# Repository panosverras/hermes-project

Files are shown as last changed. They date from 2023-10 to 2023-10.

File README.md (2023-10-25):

# HERMES project
WRO2023 Future Innovators project (smartbirds team)

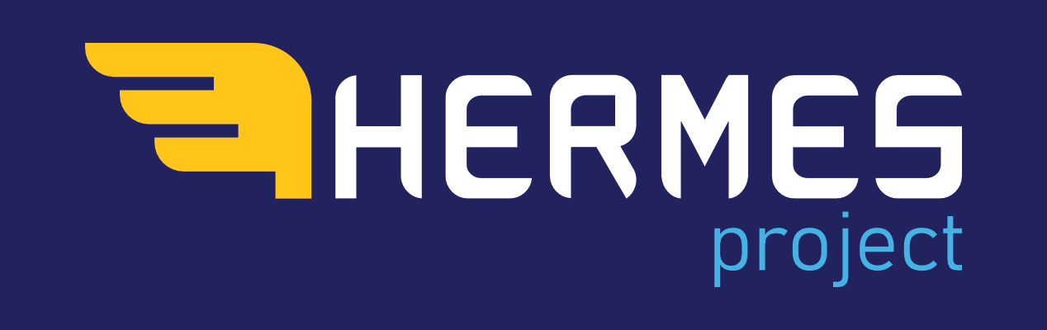
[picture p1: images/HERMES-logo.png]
HERMES logo


HERMES is a project created by **smartbirds** team (Greece) for their participation to the World Robot Olympiad 2023.
Team consists of 3 high school students, Niobe, Thymios, Faidon and their coach Mr. Panos Verras.

You can watch a short introduction of our project [here](https://www.youtube.com/watch?v=-QXrDMuEW-o).

Our project is open-source under the MIT licence. Feel free to copy, modify, reproduce in order to create a better world!

## Why we created HERMES?

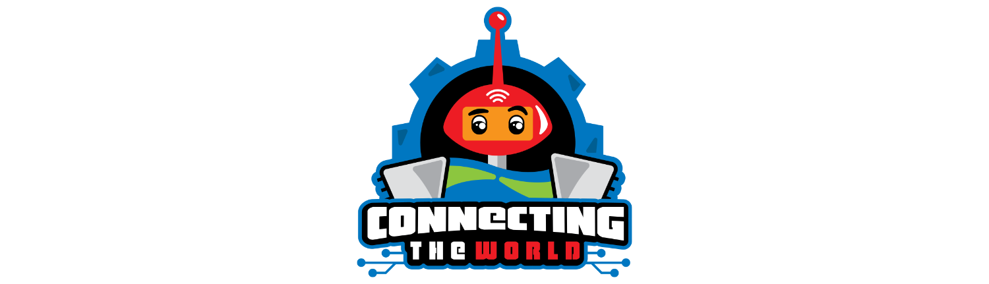
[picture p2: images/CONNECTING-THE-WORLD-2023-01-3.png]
WRO2023 theme - Connecting the World


After lots of research on this season’s theme “Connecting the World”, we came to the idea of HERMES, a multifunctional robotic system that maintains a more stable telecommunication network/infrastructure working as single node (p2p) or in combination with other units (HERMES mesh network). HERMES is based on our research on the fields of today’s IT infrastructure, undersea cable networks, socio-economic impact of IT on our daily life, marine traffic, ship design, underwater and overwater scientific and climate data and UN Sustainability Goals.

Since the beginning of time, waterways have played an important role in human communications, linking geographies and societies far and wide. Today, water not only facilitates transportation and trade but also connects nations and continents across the globe through the worldwide system of computer networks. The internet connects over 5 billion people around the world, with an impressive 99% of data being transferred through undersea fiber-optic cables. Damage on the physical underwater infrastructure could cause a multitude of problems due to internet outage, especially in cases of remote areas where an entire community relies on a few cables or even just one.

Every year, the underwater communication network undergoes between 100 and 150 faults. Most of these cable faults occur in water depths shallower than 200 meters, within a distance of approximately 1000 meters from the coastline. The internet downtime period resulting from cable faults depends on weather and climate conditions and it may take up to several months for a complete repair. Moreover, as global overseas shipping continues to grow and thus traffic in shallower waters surges, cable incidents and pollution will only increase, especially in congestion points, such as canals and rivers.

Loss of internet connectivity presents significant challenges for nations, governments and everyday people. However, the complete absence of internet access in remote regions is equally detrimental. Extending internet access to remote areas ultimately gives these communities access to vital resources and services by helping them connect to the rest of the world.

The problems arising from lack of internet access are numerous and complex, so innovative ideas and advanced technologies are the solution. Our project, HERMES, can help.

HERMES is an innovative robotic solution designed to act as a data bypass link in the event of an undersea cable fault, ensuring uninterrupted data flow. HERMES can also replace the role of underwater fiber-optic cables near the shore and therefore open valuable sea lanes that were restricted to protect those cables. Additionally, HERMES can provide an internet connection to remote regions. The robot also has environmental monitoring functions and other capabilities which focus on its surroundings.

## HERMES key features

**Wireless Network Technology:** The central idea behind this robotic solution is to decrease the possibility of cable damage, by replacing the cable communications with a wireless network, until repaired or permanently.
**Navigation and Bypass:** HERMES is able to navigate to the coordinates of the accident and bypass the communication.
**Network Extender for Remote Areas:** A system that can also run as a network extender for unreachable remote areas.
**Environmental Monitoring:** Additionally, our model operates as a station to collect data and monitor the environment, in order to identify environmental anomalies and spot air and water pollution.
**Safety in water:** Hermes can warn vessels and assist in search and rescue missions by detecting the presence of living organisms.

## How we created HERMES
HERMES system consists of 3 parts, although its name was given by the main vessel. 

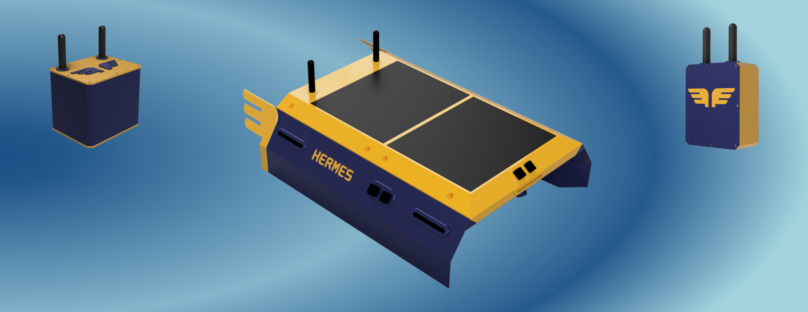
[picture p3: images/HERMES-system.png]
HERMES system


All 3 subsystems where designed in Fusion 360 and 3D printed. Due to restrictions on printing volume but also on our concept of using two colors, these susbsystems consist of several parts. In folder Design/STL you can find all these parts organized by the subsystem name. Using those files you will be able to slice and print an exact copy of HERMES, land station and underwater station. Indicatively, printing time required is more than 200 hours on a low-cost printer (like the one we used). We have rendered a small video demonstrating the assembly steps for the HERMES vessel (find it under Videos folder).

Raspberry Pi PICO is used as the main controller on all subsystems. Especially HERMES included two of them in order to balance proccessing speed and control in a better way all its functionalities. Programming language used is Python and in specific controllers are using [Circuitpython](https://circuitpython.org/) that is a user-friendly python version dedicated to micro-controllers. In folder Code you can find our programs for its one of the subsystems. Please mention that HERMES includes two PICO's so you will find two programs in that folder.

Electronics used are from several manufacturers, depending on their capabilities, their availability and our purpose (present our idea at WRO2023). Below you may find a list of the ones we used and a diagram for their connection.

### HERMES
- 2x Rasperry Pi PICO
- 2x Pico expansion board
- 3x IIC to UART module
- 4x HC12 RF module
- 4x RF waterproof antenna
- 1x PH sensor kit
- 1x Conductivity sensor kit
- 1x DS18B20 waterproof sensor
- 1x TSL2591 sensor
- 1x BME680 sensor
- 1x MQ135 sensor
- 1x GPS module
- 1x BNO 055 Euler angles sensor
- 1x Thernal imaging camera
- 2x Solar panel 3.5W
- 2x Solar power manager 10000mAh
- 1x DC step-down 5v dual usb
- 1x Dual motor driver module
- 2x thruster (dc motor)

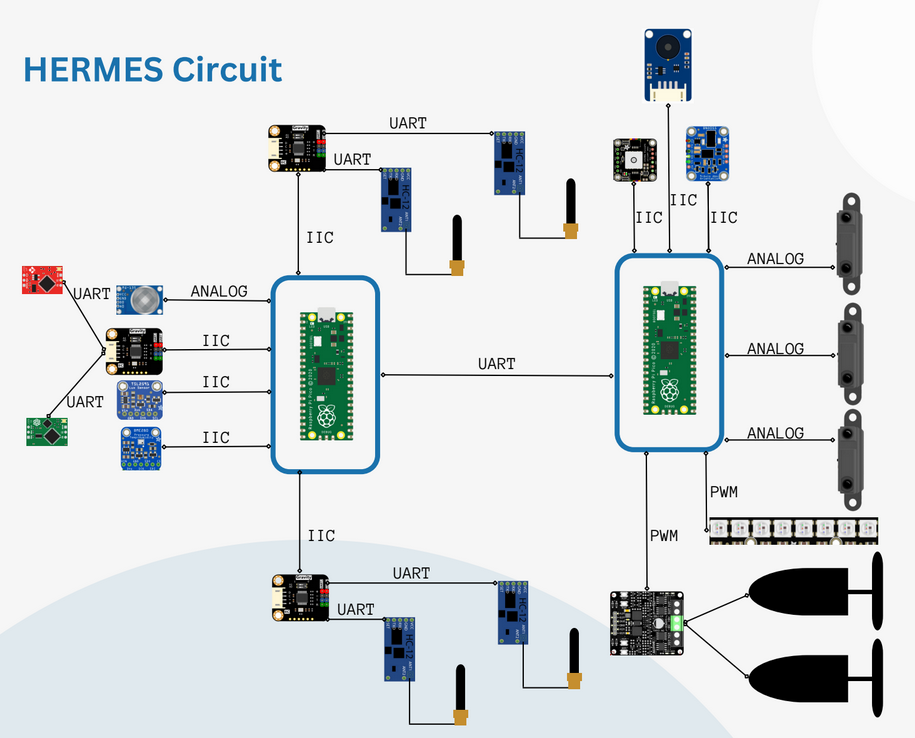
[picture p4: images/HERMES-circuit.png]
HERMES circuit


### LAND station
- 1x Rasperry Pi PICO
- 1x Pico expansion board
- 2x HC12 RF module
- 4x RF waterproof antenna

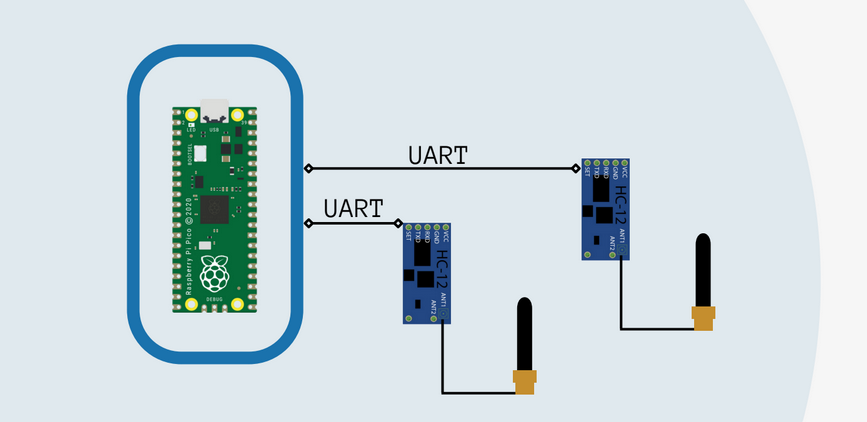
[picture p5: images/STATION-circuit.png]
LAND station circuit


### UNDERWATER station
- 1x Rasperry Pi PICO
- 1x Pico expansion board
- 2x HC12 RF module
- 4x RF waterproof antenna

LAND station circuit

## Innovation and social impact of HERMES
HERMES is a truly innovative addition to today's interconnected society. 

**Safety and Reliability for Users:** HERMES aims to increase the safety and reliability of telecom systems for users, making essential everyday networks more secure and with a steadier infrastructure.

**A Global Transformation:** Our vision is to alter worldwide communications for the better, by establishing the most stable transmission system ever. 

**Rapid Deployment and Integration:** Being a low cost and open source project it allows the rapid deployment and integration into the global internet infrastructure.

Humankind now can rely on this stable communication network for critical sectors of daily life such as good health and well being (goal 3), quality education (goal 4), reduced inequalities (goal 10), decent work and economic growth (goal 8) and many more.

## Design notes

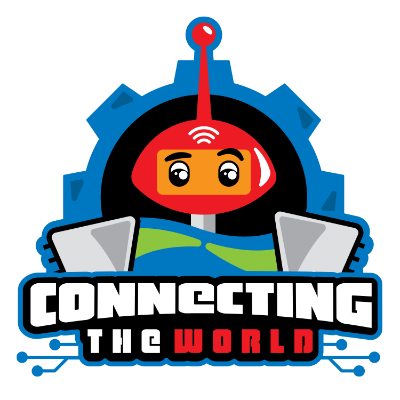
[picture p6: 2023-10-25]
images/CONNECTING-THE-WORLD-2023-01-1.png

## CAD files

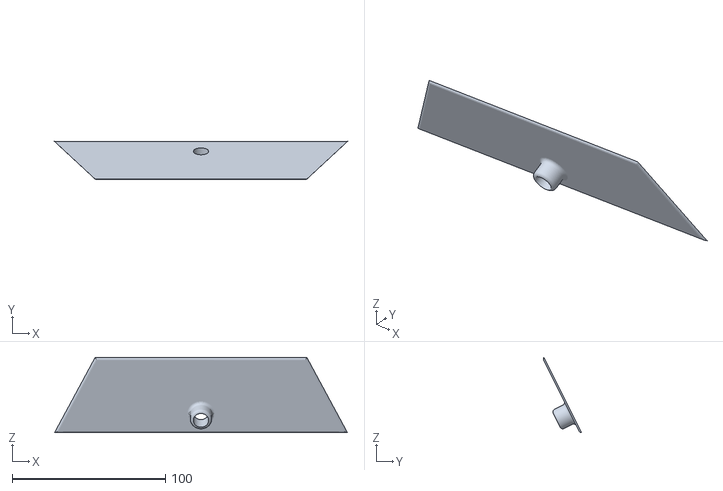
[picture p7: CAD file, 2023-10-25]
Design/STL/HERMES/BRIDGE/FRONT-MASK.stl
191.1 x 24.9 x 49.1

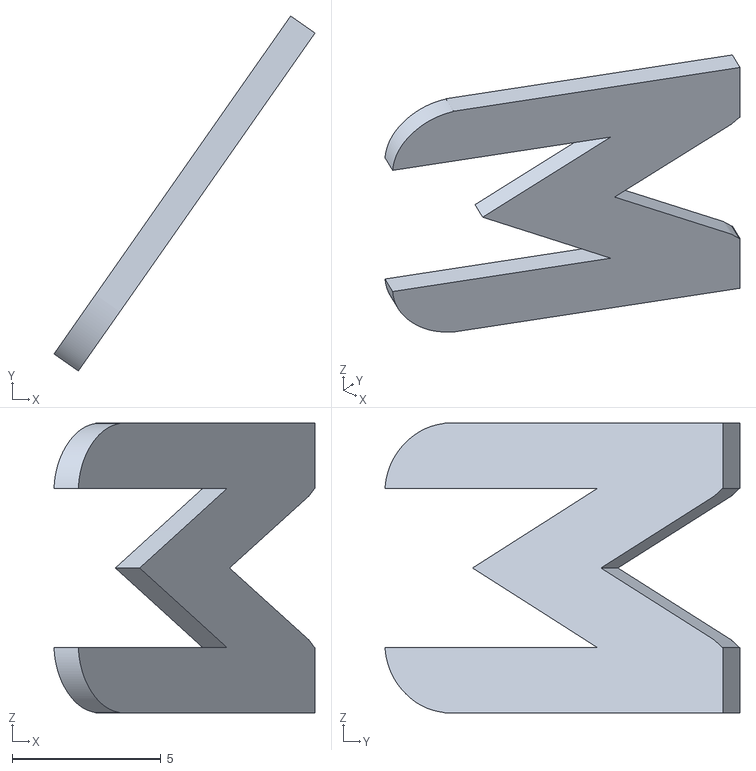
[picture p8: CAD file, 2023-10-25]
Design/STL/HERMES/DECORATIVES/M.stl
8.78 x 11.9 x 9.74

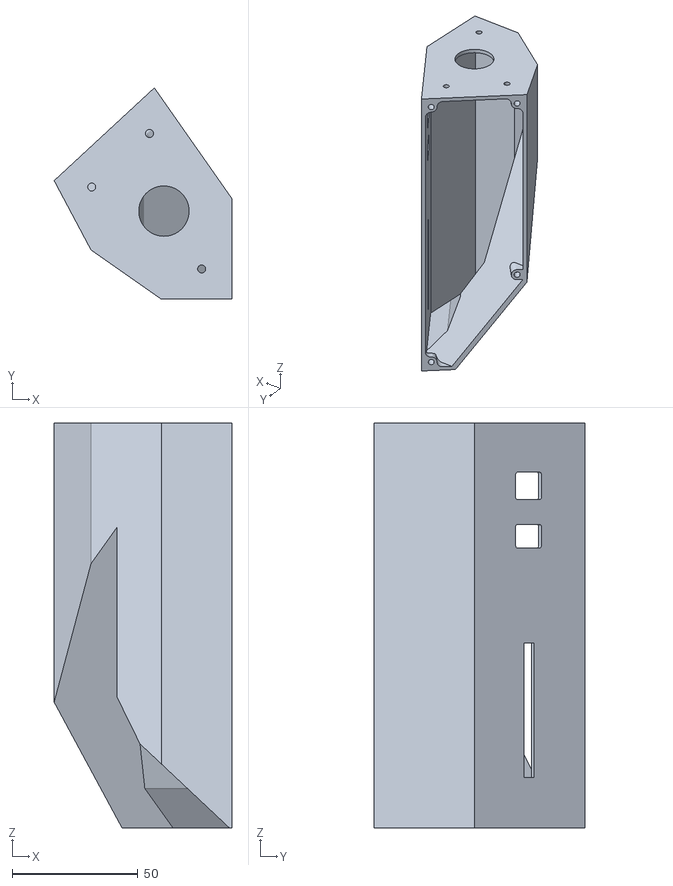
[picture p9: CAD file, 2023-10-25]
Design/STL/HERMES/HULL/HULL-FRONT-RIGHT.stl
70.6 x 84.0 x 161.0

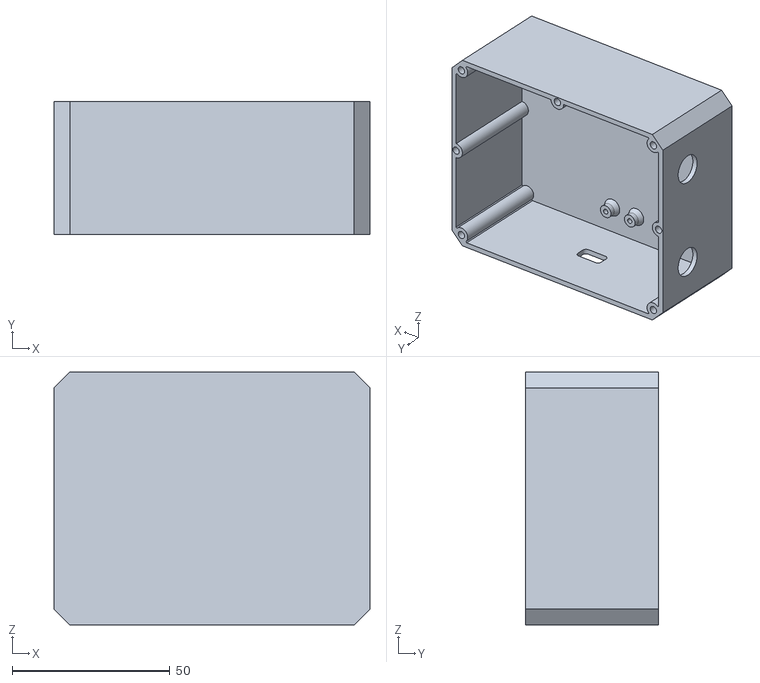
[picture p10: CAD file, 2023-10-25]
Design/STL/LANDBOX/Y-BOX.stl
100.0 x 42.0 x 80.0

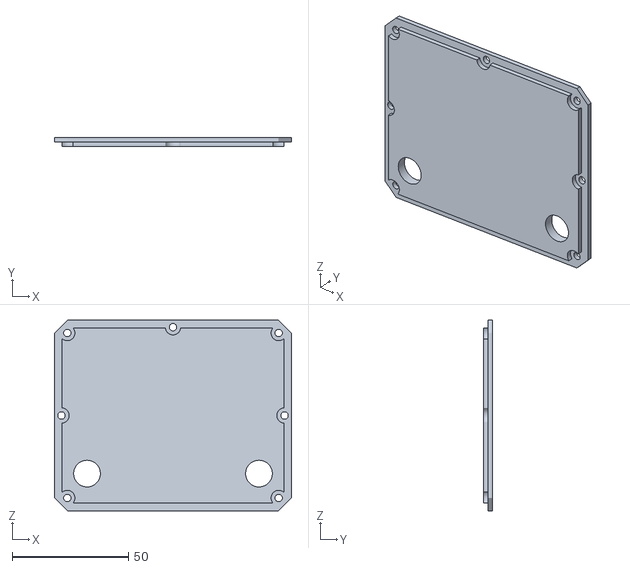
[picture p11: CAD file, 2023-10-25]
Design/STL/SEABOX/Y-TOP-LID.stl
102.0 x 4.00 x 82.0

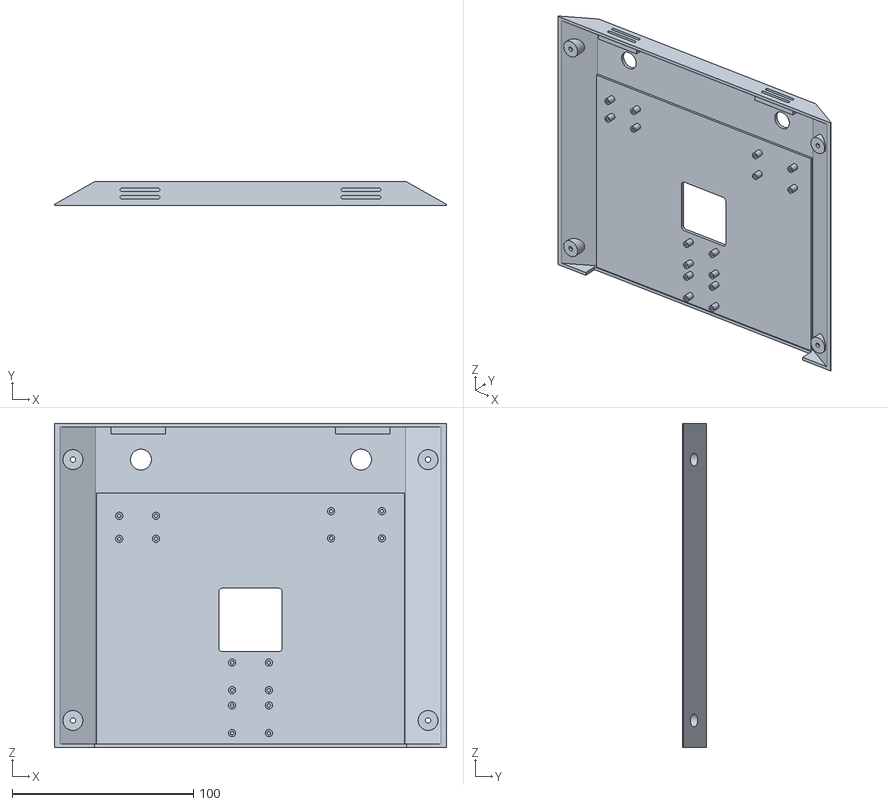
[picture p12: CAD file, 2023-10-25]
Design/STL/HERMES/BRIDGE/BACK-COVER.stl
216.4 x 13.1 x 179.0

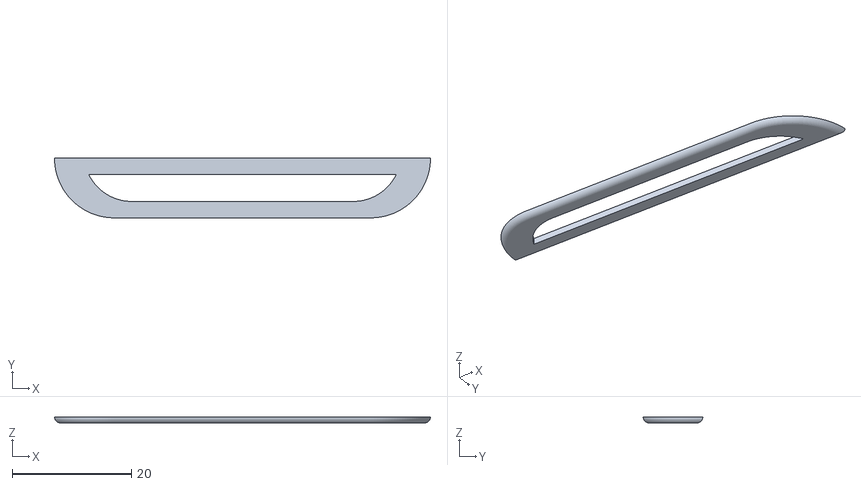
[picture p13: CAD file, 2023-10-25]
Design/STL/HERMES/DECORATIVES/MOUTH.stl
63.0 x 10.0 x 1.00

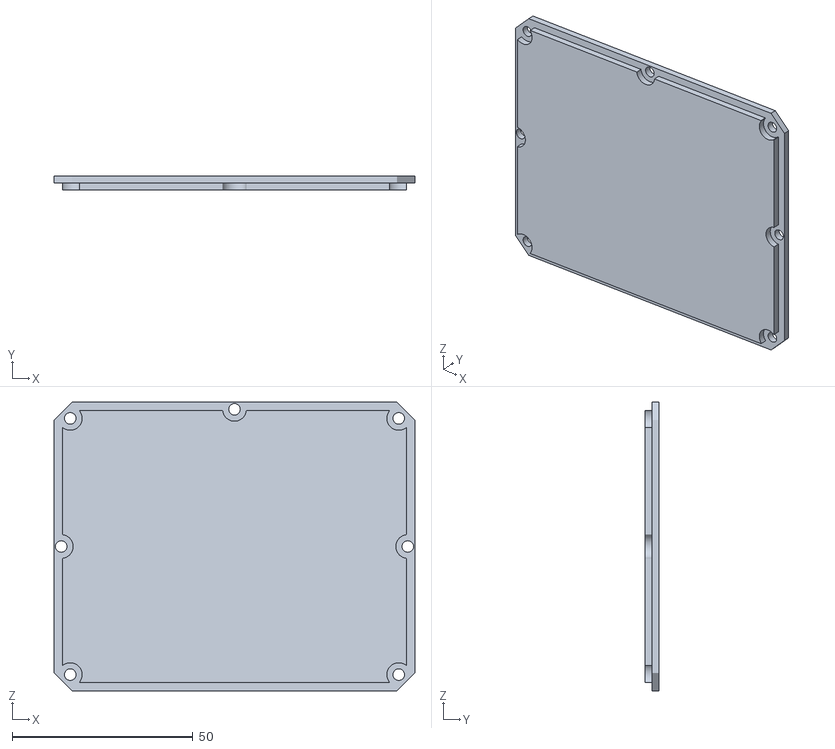
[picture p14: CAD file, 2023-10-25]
Design/STL/LANDBOX/B-LID.stl
100.0 x 4.00 x 80.0

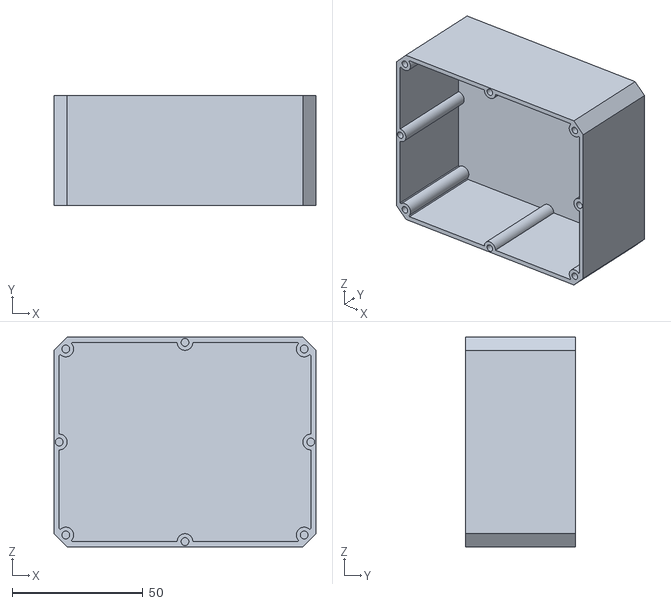
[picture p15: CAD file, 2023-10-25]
Design/STL/SEABOX/B-BOX-LOWER.stl
100.0 x 42.0 x 80.0

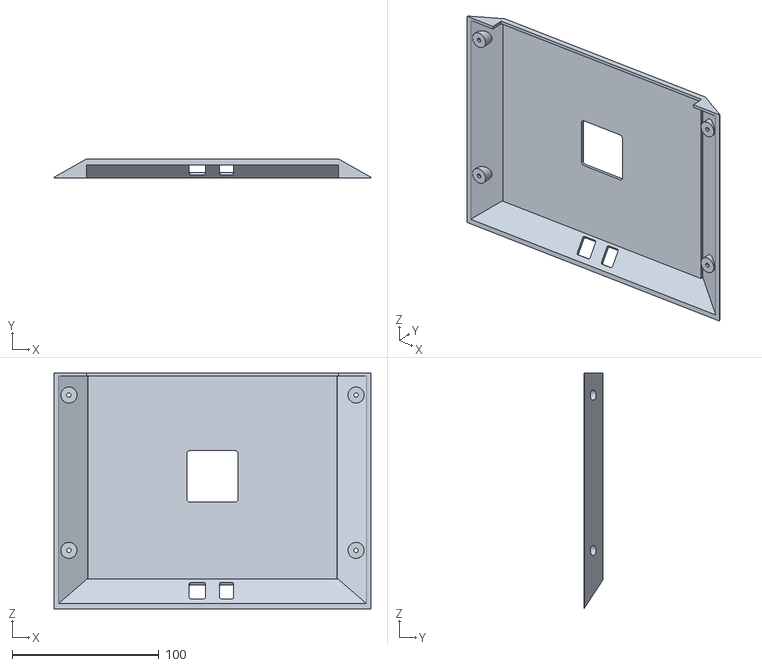
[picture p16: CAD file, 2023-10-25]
Design/STL/HERMES/BRIDGE/FRONT-COVER.stl
216.4 x 13.1 x 161.0

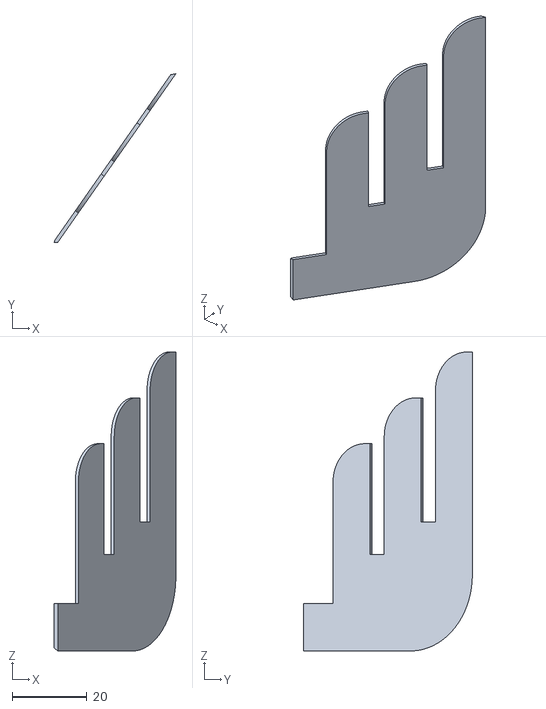
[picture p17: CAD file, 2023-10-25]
Design/STL/HERMES/DECORATIVES/LEFT-LOGO.stl
32.5 x 45.0 x 79.8

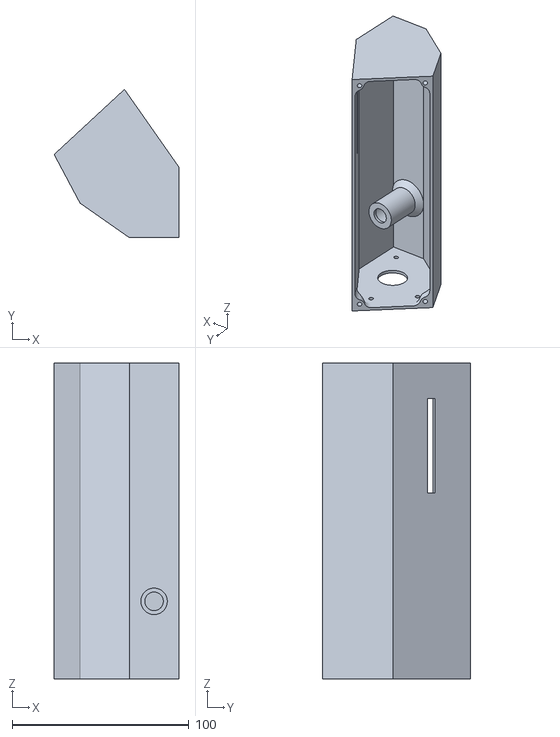
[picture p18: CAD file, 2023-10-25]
Design/STL/HERMES/HULL/HULL-REAR-RIGHT.stl
70.6 x 84.0 x 179.0

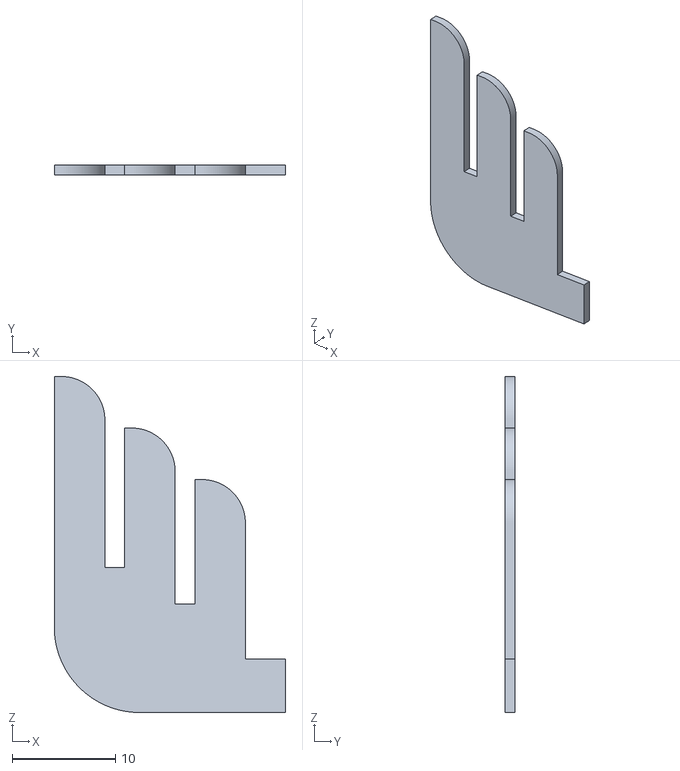
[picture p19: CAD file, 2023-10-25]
Design/STL/LANDBOX/Y-LOGO.stl
22.4 x 1.00 x 32.5

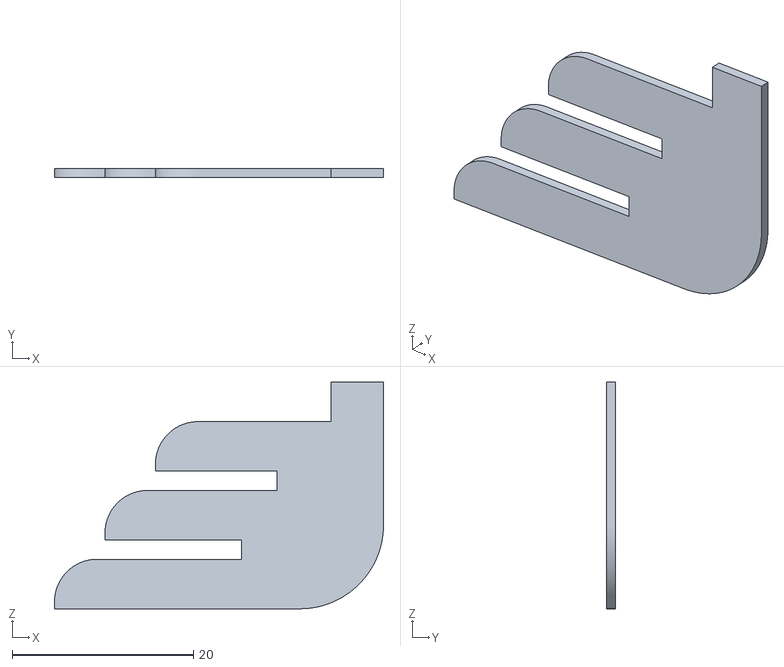
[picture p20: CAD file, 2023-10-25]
Design/STL/SEABOX/B-LOGO.stl
36.3 x 1.00 x 25.0

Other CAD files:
Design/STL/HERMES/HULL/HULL-FRONT-LEFT.stl
Design/STL/HERMES/BRIDGE/HULL-COVER-FRONT.stl
Design/STL/HERMES/DECORATIVES/RIGHT-LOGO.stl
Design/STL/HERMES/HULL/SIDE-USONIC-FRAME.stl
Design/STL/HERMES/BRIDGE/BACK-LID.stl
Design/STL/HERMES/BRIDGE/BACK-SENSOR-COVER.stl
Design/STL/HERMES/BRIDGE/FRONT-LID.stl
Design/STL/HERMES/BRIDGE/HC12-BOTTOM-COVER.stl
Design/STL/HERMES/BRIDGE/HULL-COVER-REAR.stl
Design/STL/HERMES/BRIDGE/LIQUID-SENSOR-CASE.stl
Design/STL/HERMES/BRIDGE/PBANK-HOLDER.stl
Design/STL/HERMES/BRIDGE/SUNGLASSES.stl
Design/STL/HERMES/DECORATIVES/ANTENNA-COVER.stl
Design/STL/HERMES/DECORATIVES/E..stl
Design/STL/HERMES/DECORATIVES/H.stl
Design/STL/HERMES/DECORATIVES/LEFT-LOGO-EXT.stl
Design/STL/HERMES/DECORATIVES/R.stl
Design/STL/HERMES/DECORATIVES/RIGHT-LOGO-EXT.stl
Design/STL/HERMES/DECORATIVES/S.stl
Design/STL/HERMES/HULL/HULL-REAR-LEFT-2.stl
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

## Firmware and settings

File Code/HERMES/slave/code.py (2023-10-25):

""" Loading libraries/modules -------------------------------- """
from time import sleep
from adafruit_motor import motor
import adafruit_mlx90640
import adafruit_gps
import adafruit_bno055
import neopixel
import board, digitalio, analogio, pwmio, busio, asyncio, time
# -------------------------------------------------------------- #

""" Initialising sensors/modules ----------------------------- """

# IIC sensors -------------------------------------------------- #
i2c = busio.I2C(board.GP9, board.GP8)
bno055 = adafruit_bno055.BNO055_I2C(i2c)
mlx = adafruit_mlx90640.MLX90640(i2c)
mlx.refresh_rate = adafruit_mlx90640.RefreshRate.REFRESH_2_HZ
gps_iic = adafruit_gps.GPS_GtopI2C(i2c, debug=False)
gps_iic.send_command(b"PMTK314,0,1,0,1,0,0,0,0,0,0,0,0,0,0,0,0,0,0,0")
gps_iic.send_command(b"PMTK220,1000")
# -------------------------------------------------------------- #

# UART communication ------------------------------------------- #
pico = busio.UART(board.GP4, board.GP5)
# -------------------------------------------------------------- #

# Analog sensors ----------------------------------------------- #
ultrasonic_r = analogio.AnalogIn(board.A0) #GP26
ultrasonic_l = analogio.AnalogIn(board.A1) #GP27
ultrasonic_f = analogio.AnalogIn(board.A2) #GP28
# -------------------------------------------------------------- #

# Neopixel ----------------------------------------------------- #
pixels_pin = board.GP19
pixels_num = 40
pixels = neopixel.NeoPixel(pixels_pin, pixels_num)

pixel_colors = {
    'yellow': (255, 140, 0),
    'blue': (0, 0, 150),
    'white': (150, 150, 150),
    'red': (150, 0, 0),
    'off':(0, 0, 0)
    }
# -------------------------------------------------------------- #

# Thrusters ---------------------------------------------------- #
# PWM ---------------------------------------------------------- #
in1 = pwmio.PWMOut(board.GP0, frequency=50)
in2 = pwmio.PWMOut(board.GP1, frequency=50)
in3 = pwmio.PWMOut(board.GP2, frequency=50)
in4 = pwmio.PWMOut(board.GP3, frequency=50)

motor_a = motor.DCMotor(in1, in2)
motor_b = motor.DCMotor(in3, in4)
# ------------------------------------------------------------- #

""" Helper methods ------------------------------------------ """

async def signal(mc, color=pixel_colors["white"]):
    dot_lenght = 0.25
    dash_lenght = (dot_lenght * 3)
    morse_codes = {
        "K": ("-.-"), #I wish to communicate with you
        "L": (".-.."), #You should stop your vessel instantly
        "U": ("..-"), #You are running into danger
        "CB": ("-.-. -..."), #I require immediate assistance
        "IL": (".. ._.."), #I can only proceed at slow speed
        "FO": (".._. ---"), #I will keep close to you
        "NG": ("-. __."), #You are in a dangerous position
        "SOS": ("... --- ..."), #Save Our Ship
    }

    if mc in morse_codes:
        for e in morse_codes[mc]:
            for _ in range(0,15,2):
                pixels[_] = pixel_colors['yellow']
            if e == '.':
                await asyncio.sleep(dot_lenght)
            else:
                await asyncio.sleep(dash_lenght)
            for _ in range(0,40):
                if _ != 20:
                    pixels[_] = pixel_colors["off"]
            await asyncio.sleep(dot_lenght)
            await teeth([20,], pixel_colors["blue"])
        for e in morse_codes[mc]:
            for _ in range(24,40,2):
                pixels[_] = pixel_colors['yellow']
            if e == '.':
                await asyncio.sleep(dot_lenght)
            else:
                await asyncio.sleep(dash_lenght)
            for _ in range(0,40):
                if _ != 20:
                    pixels[_] = pixel_colors["off"]
            await asyncio.sleep(dot_lenght)
            await teeth([20,], pixel_colors["blue"])
        return True
    else:
        return False


async def teeth(t, c):
    pixels.fill(pixel_colors["off"])
    for tooth in t:
        pixels[tooth] = c


async def analog_to_cm(side):
    old_range = (8000 - 46000)
    new_range = (150 - 20)
    if side == "f":
        r = (((ultrasonic_f.value - 46000) * new_range) / old_range) + 20
    elif side == "r":
        r = (((ultrasonic_r.value - 46000) * new_range) / old_range) + 20
    elif side == "l":
        r = (((ultrasonic_l.value - 46000) * new_range) / old_range) + 20
    else:
        r = "unknown side"
    return round(r, 1)


async def thruster(motor, direction, speed=1.0):
    if motor == "R":
        if direction == "r":
            motor_a.throttle = speed
            await asyncio.sleep(0.3)
            motor_b.throttle = speed
        elif direction == "l":
            motor_a.throttle = -speed
            await asyncio.sleep(0.3)
            motor_b.throttle = -speed
        else:
            motor_a.throttle = 0.0
    elif motor == "L":
        if direction == "r":
            motor_b.throttle = speed
            await asyncio.sleep(0.3)
            motor_a.throttle = speed
        elif direction == "l":
            motor_b.throttle = -speed
            await asyncio.sleep(0.3)
            motor_a.throttle = -speed
        else:
            motor_b.throttle = 0.0


async def turn(target_orientation):
    if target_orientation in range(0,360):
        current_orientation = bno055.euler[0]
        angular_distance = ((target_orientation - current_orientation + 540)% 360)-180
        if angular_distance > 20:
            await thruster("R","r", 0.1)
        elif angular_distance < -20:
            await thruster("L","r", 0.1)
        while abs(angular_distance) > 20:
            current_orientation = bno055.euler[0]
            angular_distance = ((target_orientation - current_orientation + 540)% 360)-180
            await asyncio.sleep(0.1)
        await thruster("R","s")
        await thruster("L","s")
        return True
    else:
        return False


async def forward(wait, speed=0.1):
    motor_a.throttle = speed
    await asyncio.sleep(0.3)
    motor_b.throttle = -speed
    await asyncio.sleep(wait)
    motor_a.throttle = 0
    motor_b.throttle = 0


async def gps(msg):
    gps_iic.update()
    if gps_iic.has_fix:
        if msg == "lat":
            r = gps_iic.latitude
        elif msg == "lon":
            r = gps_iic.longitude
        elif msg == "head":
            r = gps_iic.track_angle_deg
    else:
        if msg == "head":
            r = bno055.euler[0]
        else:
            r = "NO FIX"
    return r


async def camera():
    frame = [0] * 768
    count = 0
    try:
        mlx.getFrame(frame)
    except ValueError as e:
        print(e)
    for h in range(24):
        for w in range(32):
            t = frame[h * 32 + w]
            if t > 30:
                count += 1
    print(count)
    if count > 300:
        r = "Object found\n"
    else:
        r = "Everything ok\n"
    return r


async def pico_t(msg):
    pico.write(msg.encode())
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

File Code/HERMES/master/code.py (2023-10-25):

# Loading libraries/modules ------------------------------------ #

from time import sleep
import asyncio
import adafruit_ds18x20, digitalio, adafruit_mlx90640
from adafruit_onewire.bus import OneWireBus
import board, busio, adafruit_bme680, adafruit_tsl2591, analogio
import circuitpython_dfrobot_gravity_drf0627_dual_uart as DualUart
# -------------------------------------------------------------- #

# Initialising sensors/modules --------------------------------- #

# IIC sensors -------------------------------------------------- #
i2c = busio.I2C(board.GP5, board.GP4)
bme680 = adafruit_bme680.Adafruit_BME680_I2C(i2c)
tsl = adafruit_tsl2591.TSL2591(i2c)
# -------------------------------------------------------------- #

# UART communication ------------------------------------------- #
pico = busio.UART(board.GP0, board.GP1)

hc12_air_out_uart = DualUart.DFRobot_IIC_Serial(i2c, sub_uart_channel=DualUart.DFRobot_IIC_Serial.SUBUART_CHANNEL_1, IA1=1, IA0=1) #yellow
hc12_air_in_uart = DualUart.DFRobot_IIC_Serial(i2c, sub_uart_channel=DualUart.DFRobot_IIC_Serial.SUBUART_CHANNEL_2, IA1=1, IA0=1) #red
hc12_sea_out_uart = DualUart.DFRobot_IIC_Serial(i2c, sub_uart_channel=DualUart.DFRobot_IIC_Serial.SUBUART_CHANNEL_1, IA1=0, IA0=1) #green
hc12_sea_in_uart = DualUart.DFRobot_IIC_Serial(i2c, sub_uart_channel=DualUart.DFRobot_IIC_Serial.SUBUART_CHANNEL_2, IA1=0, IA0=1) #blue

hc12_air_out_uart.begin(9600, hc12_air_out_uart.IIC_Serial_8N1)
hc12_air_in_uart.begin(9600, hc12_air_in_uart.IIC_Serial_8N1)
hc12_sea_out_uart.begin(9600, hc12_sea_out_uart.IIC_Serial_8N1)
hc12_sea_in_uart.begin(9600, hc12_sea_in_uart.IIC_Serial_8N1)

hc12_air_out_set = digitalio.DigitalInOut(board.GP3)
hc12_air_in_set = digitalio.DigitalInOut(board.GP12)
hc12_sea_out_set = digitalio.DigitalInOut(board.GP13)
hc12_sea_in_set = digitalio.DigitalInOut(board.GP14)

hc12_air_out_set.direction = digitalio.Direction.OUTPUT
hc12_air_in_set.direction = digitalio.Direction.OUTPUT
hc12_sea_out_set.direction = digitalio.Direction.OUTPUT
hc12_sea_in_set.direction = digitalio.Direction.OUTPUT

ph_pin = DualUart.DFRobot_IIC_Serial(i2c, sub_uart_channel=DualUart.DFRobot_IIC_Serial.SUBUART_CHANNEL_1, IA1=1, IA0=0)
cond_pin = DualUart.DFRobot_IIC_Serial(i2c, sub_uart_channel=DualUart.DFRobot_IIC_Serial.SUBUART_CHANNEL_2, IA1=1, IA0=0)
ph_pin.begin(9600, ph_pin.IIC_Serial_8N1)
cond_pin.begin(9600, cond_pin.IIC_Serial_8N1)
# -------------------------------------------------------------- #

# Analog sensors ----------------------------------------------- #
mq135 = analogio.AnalogIn(board.A0) #GP26
ultrasonic = analogio.AnalogIn(board.A2)
# -------------------------------------------------------------- #

# OneWire sensor ----------------------------------------------- #
ow_bus = OneWireBus(board.GP2)
ds18b20 = adafruit_ds18x20.DS18X20(ow_bus, ow_bus.scan()[0])
# -------------------------------------------------------------- #


""" Helper methods ------------------------------------------- """

async def get_data():
    data = "\n----------------------------------------\nTemperature: {} °C\nWater temperature: {} °C\nHumidity: {}%\n".format(round(bme680.temperature,1),round(ds18b20.temperature,1), round(bme680.humidity))
    await hc12_sea_out(data)

async def mq135_ppm(sensor_value, scale = True):
    ppm = round(sensor_value * (1000/65535), 2)
    if scale == True:
        if ppm < 700:
           quality = "Excellent"
        elif ppm >= 600 and ppm < 800:
           quality = "Good"
        elif ppm >= 800 and ppm < 1100:
            quality = "Poor"
        elif ppm >= 1100 and ppm < 1500:
            quality = "Unhealthy"
        elif ppm >= 1500 and ppm < 2000:
            quality = "Very unhealthy"
        elif ppm >= 2000 and ppm < 3000:
            quality = "Hazardous"
        elif ppm >= 3000:
            quality = "Extreme"
        r = [ppm, quality]
        return r
    else:
        return ppm

async def ph(scale=True):
    ph_pin.write("R\r")
    value = ph_pin.read(32)
    x = ""
    for _ in value:
        x += chr(_)
    ph_value = x.split("*")
    if scale == True:
            if ph_value[0] < 2.0:
               quality = "Extremely Acidic"
            elif ph_value[0] >= 2.0 and ph_value[0] < 4.0:
               quality = "Acidic"
            elif ph_value[0] >= 4.0 and ph_value[0] < 6.0:
                quality = "Slightly Acidic"
            elif ph_value[0] >= 6.0 and ph_value[0] < 8.0:
                quality = "Normal"
            elif ph_value[0] >= 8.0 and ph_value[0] < 10.0:
                quality = "Slightly Basic"
            elif ph_value[0] >= 10.0 and ph_value[0] < 12.0:
                quality = "Basic"
            elif ph_value[0] >= 12.0:
                quality = "Extremely Basic"
            r = [ph_value[0], quality]
            return r
    else:
        return ph_value[0]


async def conductivity():
    cond_pin.write("R\r")
    value = cond_pin.read(32)
    r = ""
    for _ in value:
        r += chr(_)
    responce = r.split("*")
    return responce[0]
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
